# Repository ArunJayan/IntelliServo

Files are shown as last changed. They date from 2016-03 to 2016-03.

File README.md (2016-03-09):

IntelliServo
===================================================================

<p align="center">
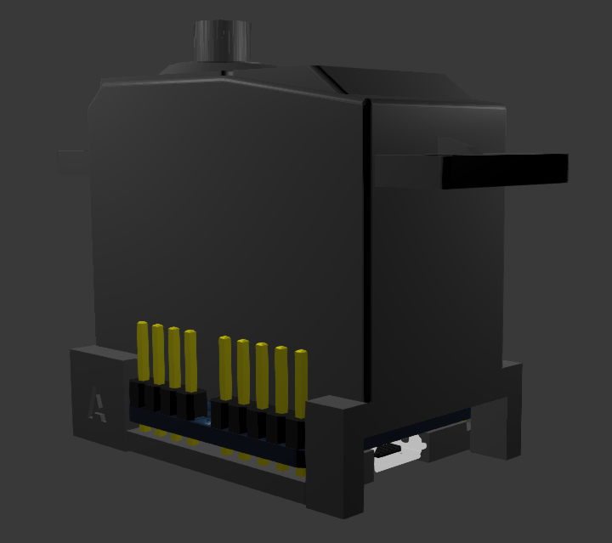
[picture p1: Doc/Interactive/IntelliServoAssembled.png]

</p>

##Overview
IntelliServo is a project aiming to transform regular hobby servos into intelligent ones by replacing their original boards. 
By doing so the servo has upgraded capabilities, such as being able to read its position, temperature and current consumption. 
Multiple servos can now be daisy-chained and controlled over I2C from a microcontroller, or over USB from a computer.

Each board features an LPC11U24 microcontroller, a DRV8837 motor driver, a TMP36 temperature sensor and a PCA9508 I2C repeater.
Each servo is unique, and so the list of compatible servos will expand with the community, so don't hesitate to add your servo!

<div style="width: 100%; display: table;">
<div style="display: table-row">

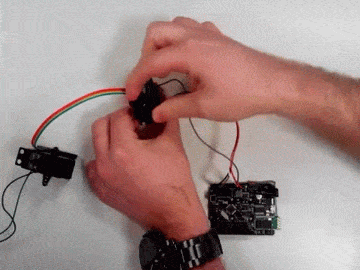
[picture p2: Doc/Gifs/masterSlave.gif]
<div align="center" style="display: table-cell;"><p align="center"><a href="https://youtu.be/W2uScJmLD4c" target="_blank">Master/Slave configuration</a></p></div>

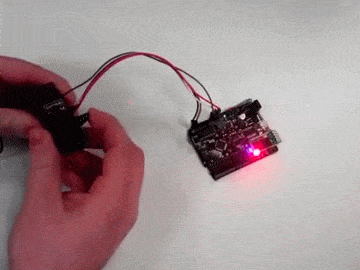
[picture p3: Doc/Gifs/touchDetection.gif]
<div align="center" style="display: table-cell;">
<p align="center"><a href="https://youtu.be/FjYgxcrhwy4" target="_blank">Touch detection</a></p>
</div>

</div>
</div>

##Connections
V_BAT: Main power line, energizes the motor and all the servo's ICs. Works between 5 and 12 volts.
V_I2C: Voltage reference for the I2C bus and powers components on the auxiliary bus. Must be 3.3V or 5V.

The servo has different connector groups:
* Main bus (5 lines): It is used to power and control the servos in daisy-chain configuration, attaching each one's A side to the previous' B side.
* Auxiliary bus (4 lines): Its function is to provide an extra link to the I2C bus, to allow other devices to be used at the same time.
* Power bus (2 lines): The main bus can be powered from the power bus on any servo, or from the last servo's main bus V_BAT and GND.
* Micro USB: Used both to upload the firmware to the board as to use it to control the servo directly from the PC, without involving other microcontrollers.

<p align="center">
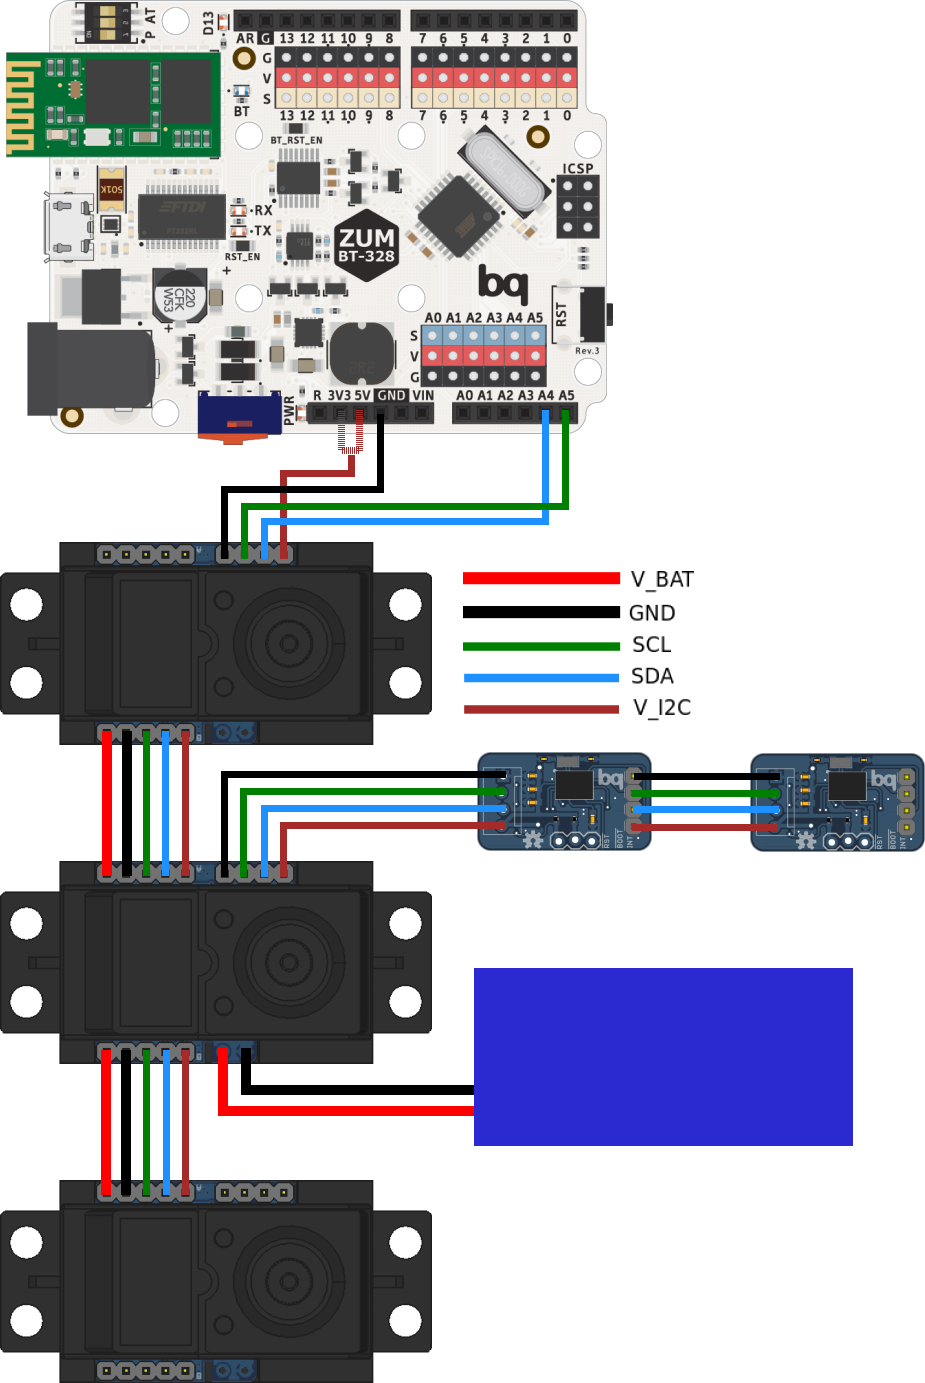
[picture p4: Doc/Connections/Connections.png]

</p>

##Installing Firmware
The board runs the firmware included in the Software/Firmware section. It is written in C++ and uses Mbed, to upload it connect the board over USB and then power it using the V_BAT and GND lines while pressing the button. 

To compile it use the "mBuino" Mbed platform, which uses the smaller LPC11U24FHI33/301 model instead of the larger LPC11U24FBD64/401 model normally used in other boards. This is important because the EEPROM memory maps are different between both and the board won't be able to access the EEPROM until the right platform is chosen.

<p align="center">
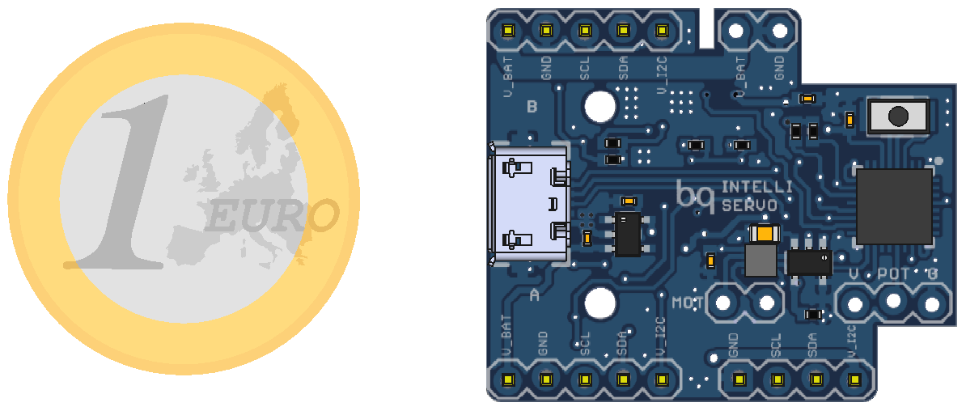
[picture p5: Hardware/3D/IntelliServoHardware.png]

</p>

##Library
The servos are controlled over I2C, but to simplify their use an arduino library with all the relevant functions and some example sketches are included as well. 
To install it simply copy it to the "sketchbook/libraries/" folder. 

##Specifications
V_BAT:&nbsp;&nbsp;&nbsp;&nbsp;&nbsp;5V-12V
V_I2C:&nbsp;&nbsp;&nbsp;&nbsp;&nbsp;&nbsp;&nbsp;3.3V/5V
I_Servo:&nbsp;&nbsp;&nbsp;&nbsp;1.8A max
I_Line:&nbsp;&nbsp;&nbsp;&nbsp;&nbsp;&nbsp;&nbsp;5A max (60mil trace)

##Contributing
This project is open-source and as so everyone is welcome to contribute. The most useful way of doing so is perhaps by expanding the list of compatible servos, by finding the moving range in degrees and PID parameters specific for each servo.

To do so add the servo to the IntelliServoConfig.h file as below

```cpp
//Added by username
#ifdef NAME_OF_SERVO
    float maxAngle=XXX;
    float Kp=XXX, Kd=XXX, Ki=XXX;
#endif
```
and to the IntelliServoMain.cpp file
```cpp
//#define NAME_OF_SERVO
```

##License
This project is licensed under Creative Commons Attribution-ShareAlike 4.0 International (CC BY-SA 4.0)

<p align="center">

</p>

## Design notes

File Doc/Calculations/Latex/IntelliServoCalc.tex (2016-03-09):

\documentclass[11pt]{article}
\usepackage[a4paper, total={17cm, 25cm}]{geometry}

\usepackage{graphicx}
\usepackage{mathtools}
\usepackage{listings}
\usepackage{color}
\definecolor{dkgreen}{rgb}{0,0.6,0}
\definecolor{gray}{rgb}{0.5,0.5,0.5}
\definecolor{mauve}{rgb}{0.58,0,0.82}
\lstset{
  language=Java,
  aboveskip=1mm,
  belowskip=1mm,
  showstringspaces=false,
  columns=flexible,
  basicstyle={\small\ttfamily},
  numbers=none,
  numberstyle=\tiny\color{gray},
  keywordstyle=\color{blue},
  commentstyle=\color{dkgreen},
  stringstyle=\color{mauve},
  breaklines=true,
  breakatwhitespace=true,
  tabsize=3
}

\begin{document}
\thispagestyle{empty}

\begin{center}
 
\hspace{-8.5cm}{
\begin{minipage}[]{\linewidth}% to keep image and caption on one page
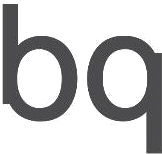
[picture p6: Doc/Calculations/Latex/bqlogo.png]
\center 
\end{minipage}
\hspace{3.5cm}Alvaro Ferr\'an Cifuentes
}

\vspace{1.75cm}
\textsc{\Huge Hardware Calculations}

\end{center}

\bigskip \flushleft

This document's purpose is to explain the current sensor calculations and the temperature sensor's equation.

\section*{Current Sensor}
Since the board uses a TI DRV8837 motor driver with a 1.8A maximum current, that is the range the LPC11U24's ADC should work in.\\[0.25cm]

To measure the current used by the motor a  10m$\Omega$ shunt resistor (R5) is added between the driver's GND pin and the ground plane. From Ohm's Law, for every 1000mA through the resistor there is a 10mV voltage drop, which means an 18mV range.\\[0.25cm]

The ADC works between 0 and 3.3V and has a 10-bit resolution, or a 3.23mV/step resolution. With this setup only the first 6 steps of the 1024 would be meaningful, which is a meager 0.6\% of the ADC's scale. 

\vspace{0.5cm}
\begin{minipage}[]{\linewidth}% to keep image and caption on one page
\center 
\end{minipage}
\\[0.5cm]

To use the ADC's full scale the resistor's voltage range must be transformed to that of the ADC, which is done by multiplying by the operational amplifier's gain G.

\center $G=\frac{3300}{18}=183.33$

\flushleft To get such gain the OpAmp is configured as a non-inverting amplifier, as seen in the following image:

\vspace{0.5cm}
\begin{minipage}[]{\linewidth}% to keep image and caption on one page
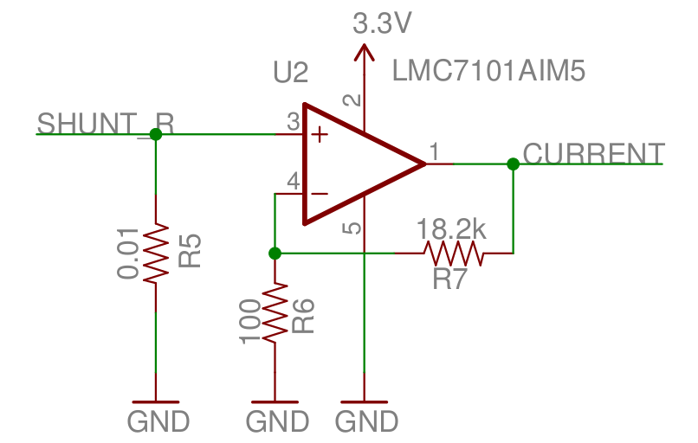
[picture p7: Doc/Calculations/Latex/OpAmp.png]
\center 
\end{minipage}
\\[0.5cm]

\center $G=1+\frac{R7}{R6}$
\center $G=1+\frac{18.2k}{100}$
\\[0.4cm]

The ADC will now use its full scale to read the current, with a theoretical resolution of 1.76mA/step.

\newpage \thispagestyle{empty}
\bigskip \flushleft

\section*{Temperature Sensor}
The board includes a TMP36 temperature sensor from Analog Devices. From its datasheet:

\vspace{0.5cm}
\begin{minipage}[]{\linewidth}% to keep image and caption on one page
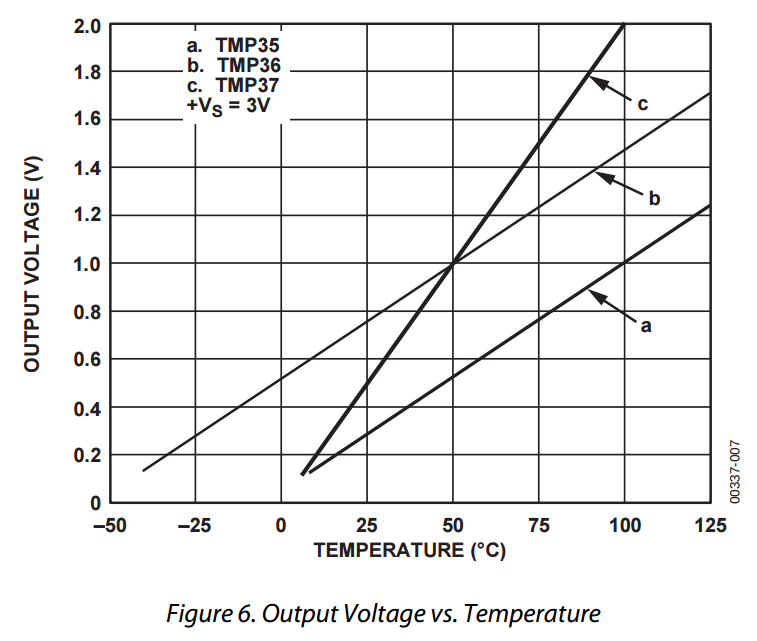
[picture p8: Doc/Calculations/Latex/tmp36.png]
\center 
\end{minipage}
\\[0.5cm]

and TMP36 Output Voltage when T=25$^\circ$C is 750mV. Knowing this, the temperature equation is calculated:

\center $V(mV)=m\cdot T(^\circ C)+p$
\center $m=\frac{1000-750}{50-25}=10$
\center $p=V-m\cdot T=750-10\cdot25=500$
\center $V(mV)=10\cdot T(^\circ C)+500$
\\[1cm]
\center $\rightarrow T(^\circ C)= (V(mV)-500)/10$

\end{document}

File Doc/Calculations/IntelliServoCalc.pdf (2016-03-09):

Alvaro Ferr´an Cifuentes

## Hardware Calculations

This document’s purpose is to explain the current sensor calculations and the temperature sensor’s equation.

## Current Sensor

Since the board uses a TI DRV8837 motor driver with a 1.8A maximum current, that is the range the LPC11U24’s ADC should work in.

To measure the current used by the motor a 10mΩ shunt resistor (R5) is added between the driver’s GND pin and the ground plane. From Ohm’s Law, for every 1000mA through the resistor there is a 10mV voltage drop, which means an 18mV range.

The ADC works between 0 and 3.3V and has a 10-bit resolution, or a 3.23mV/step resolution. With this setup only the first 6 steps of the 1024 would be meaningful, which is a meager 0.6% of the ADC’s scale.

To use the ADC’s full scale the resistor’s voltage range must be transformed to that of the ADC, which is done by multiplying by the operational amplifier’s gain G.

G =

3300
18 = 183.33

To get such gain the OpAmp is configured as a non-inverting amplifier, as seen in the following image:


G = 1 + R7
R6
G = 1 + 18.2k
100

The ADC will now use its full scale to read the current, with a theoretical resolution of 1.76mA/step.

## Temperature Sensor

The board includes a TMP36 temperature sensor from Analog Devices. From its datasheet:


and TMP36 Output Voltage when T=25◦C is 750mV. Knowing this, the temperature equation is calculated:

V (mV ) = m · T(

◦C) + p

m =

1000−750
50−25 = 10

p = V − m · T = 750 − 10 · 25 = 500

V (mV ) = 10 · T(

◦C) + 500

→ T(

◦C) = (V (mV ) − 500)/10

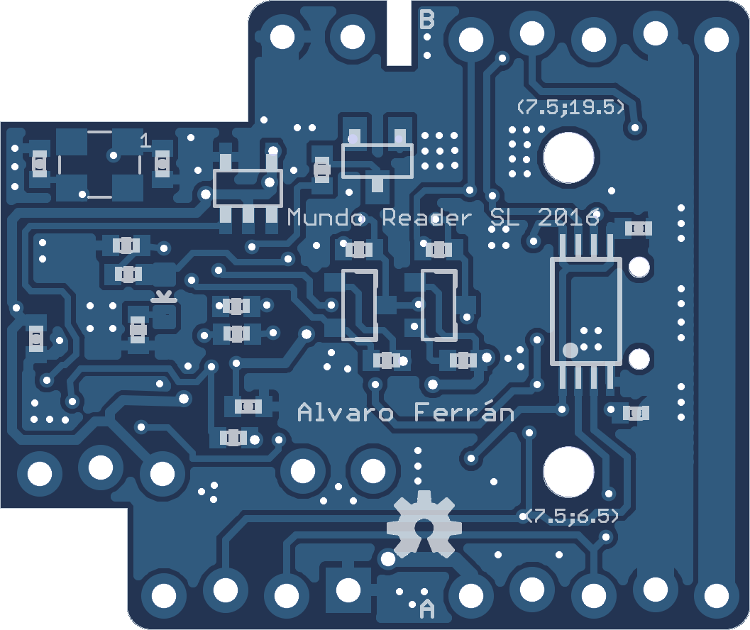
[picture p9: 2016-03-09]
Hardware/Eagle/Silkscreen/Silkscreen2-Bottom.png

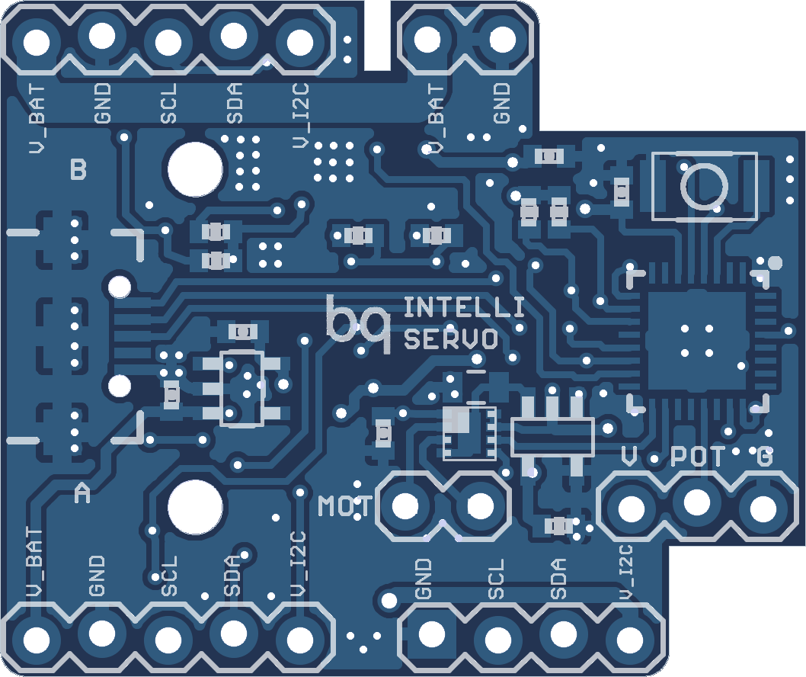
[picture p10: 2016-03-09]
Hardware/Eagle/Silkscreen/Silkscreen1-Top.png

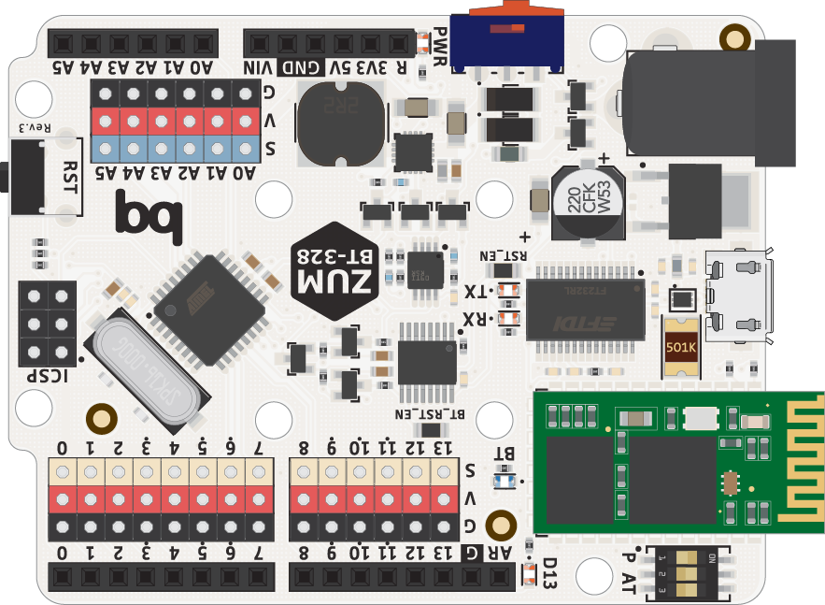
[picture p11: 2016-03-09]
Doc/Connections/DiaImgs/zumbt.png

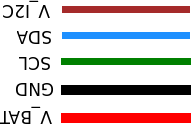
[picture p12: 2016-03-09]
Doc/Connections/DiaImgs/Legend.png

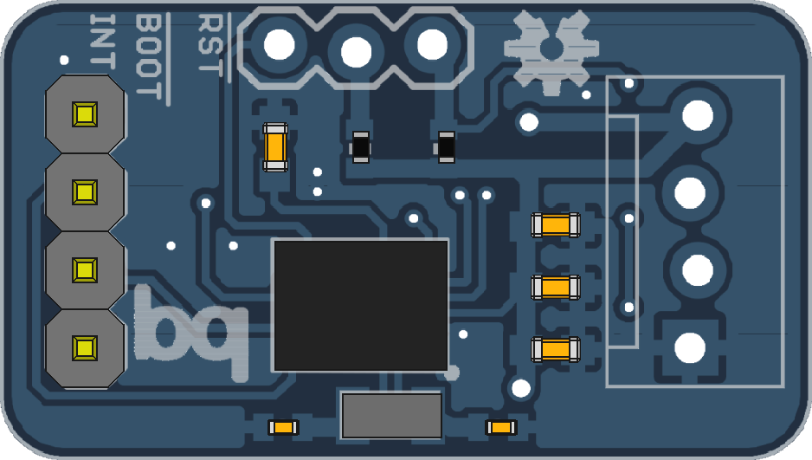
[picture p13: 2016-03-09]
Doc/Connections/DiaImgs/BNO055.png

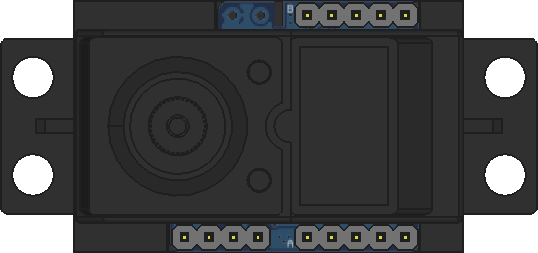
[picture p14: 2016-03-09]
Doc/Connections/DiaImgs/servo.png

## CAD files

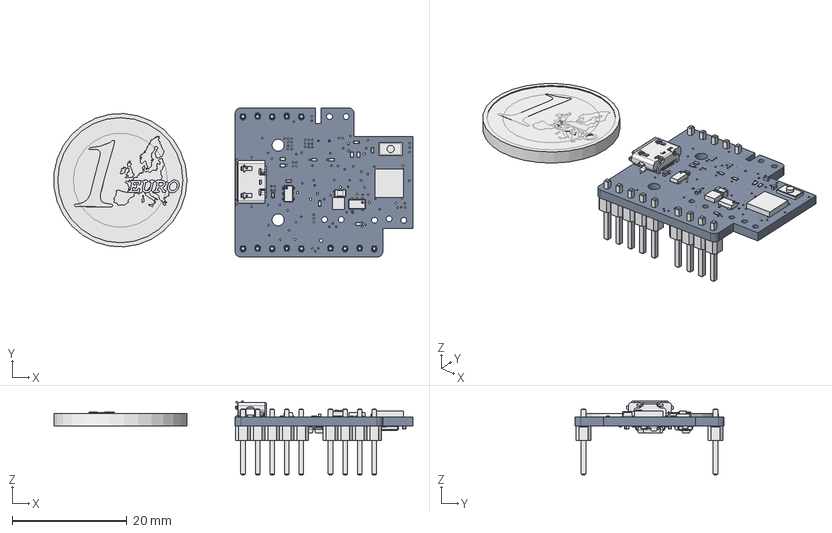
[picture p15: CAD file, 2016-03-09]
Hardware/3D/IntelliServoHardware.fcstd
62.6 x 26.0 x 12.9 mm
Board
Q2
C11
C3
C7
C8
C9
C10
C6
C4
C2
C1
C5
IC3
LED1
Q3
R5
R9
R10
R16
R15
R18
R12
R7
R6
R1
R2
R3
R4
R14
R13
R8
R11
R17
R19
SW1
U1
U2
U3
IC2
IC1
JP7
Q1
Q4
1x5pins
1x5pins001
1x4pins
Euro

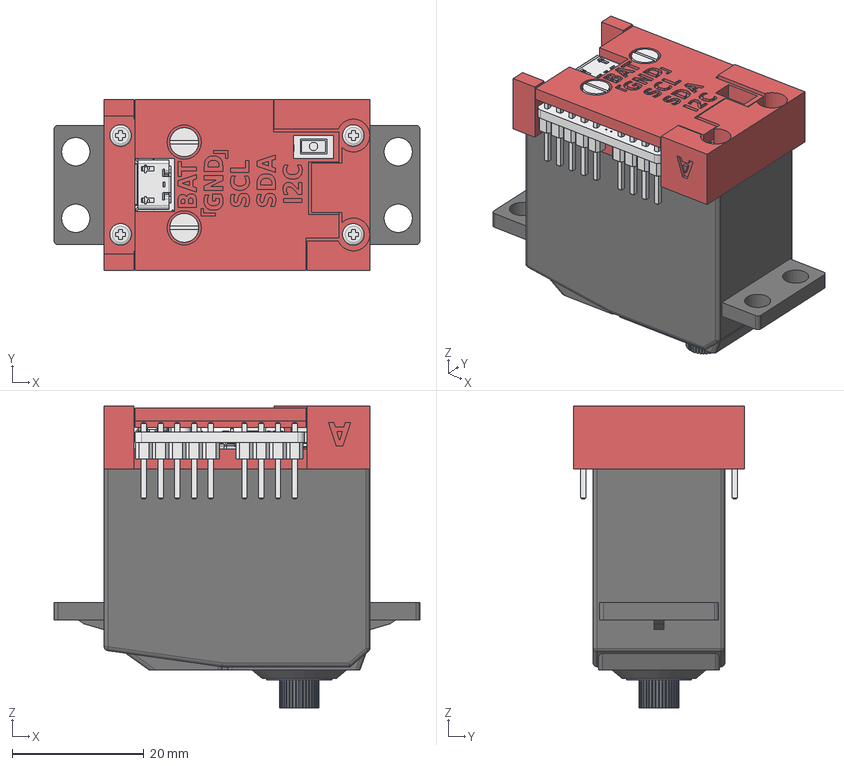
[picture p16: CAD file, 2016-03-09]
Mechanical/IntelliServoMechanical.fcstd
55.5 x 26.0 x 45.7 mm
FutabaS3003-screws
FutabaS3003
PCB-screws
base-src
cover-src
PCB

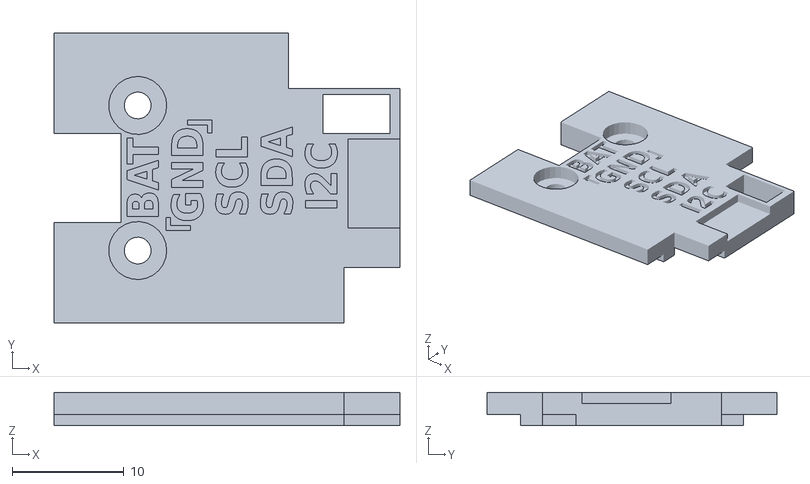
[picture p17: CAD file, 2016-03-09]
Mechanical/STL/cover.stl
31.0 x 26.0 x 3.00

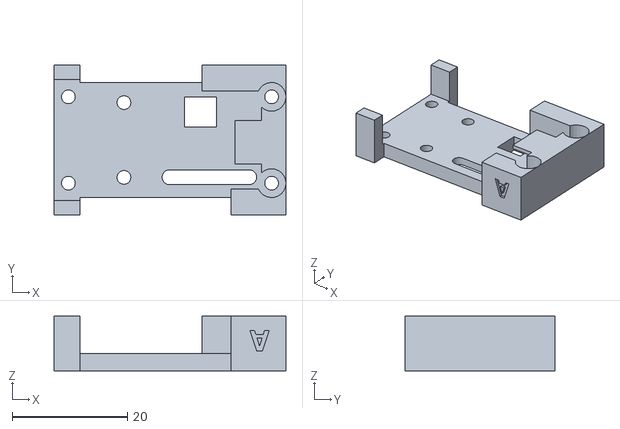
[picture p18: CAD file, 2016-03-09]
Mechanical/STL/base.stl
40.3 x 26.0 x 9.50

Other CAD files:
Hardware/Eagle/Outline/IntelliServoOutline.fcstd
Doc/Interactive/IntelliServoBoard.blend
Hardware/Eagle/Outline/IntelliServoOutline.dxf

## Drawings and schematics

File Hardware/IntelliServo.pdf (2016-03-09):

# R7 R⁶ U3

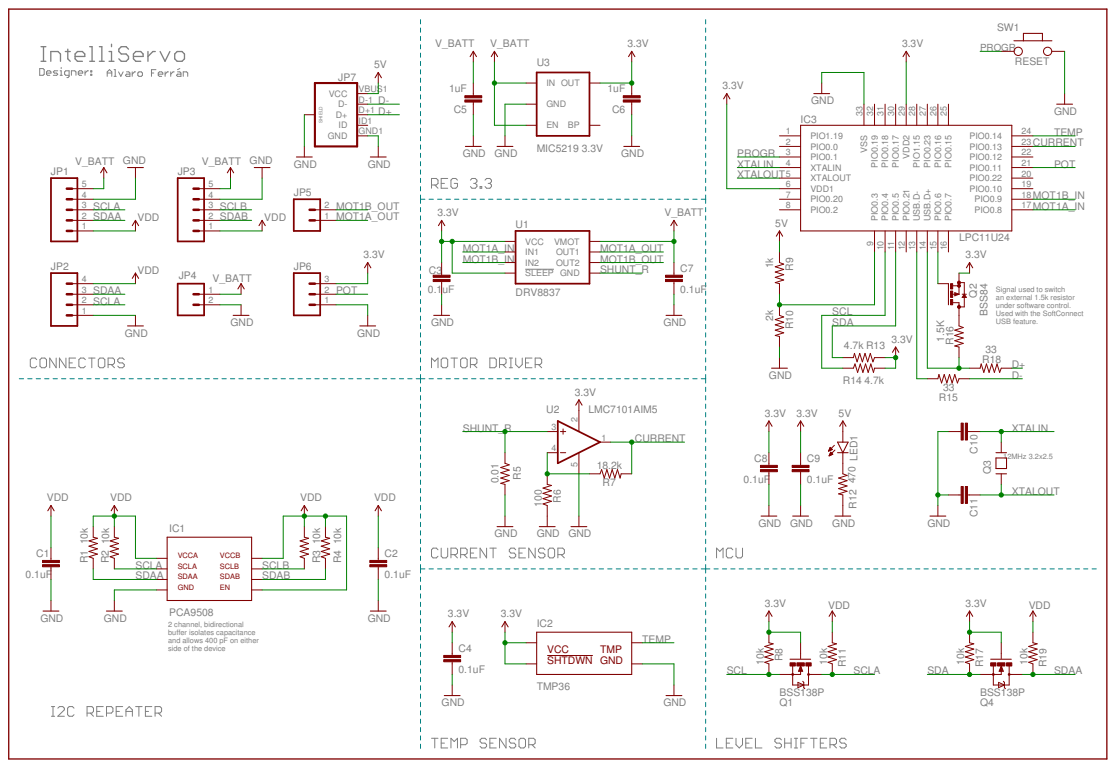
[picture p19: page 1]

BSS84
Signal used to switch
an external 1.5k resistor under software control. Used with the SoftConnect USB feature.

PCA9508
2 channel, bidirectional buffer isolates capacitance
and allows 400 pF on either side of the device

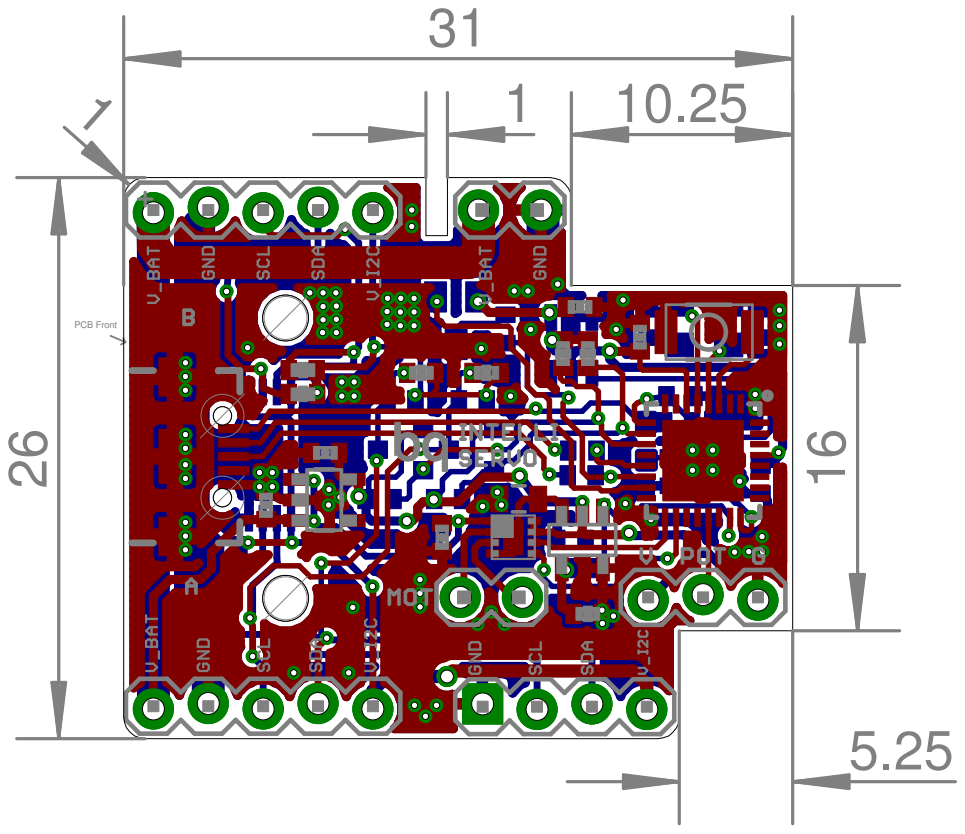
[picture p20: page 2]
PCB Front

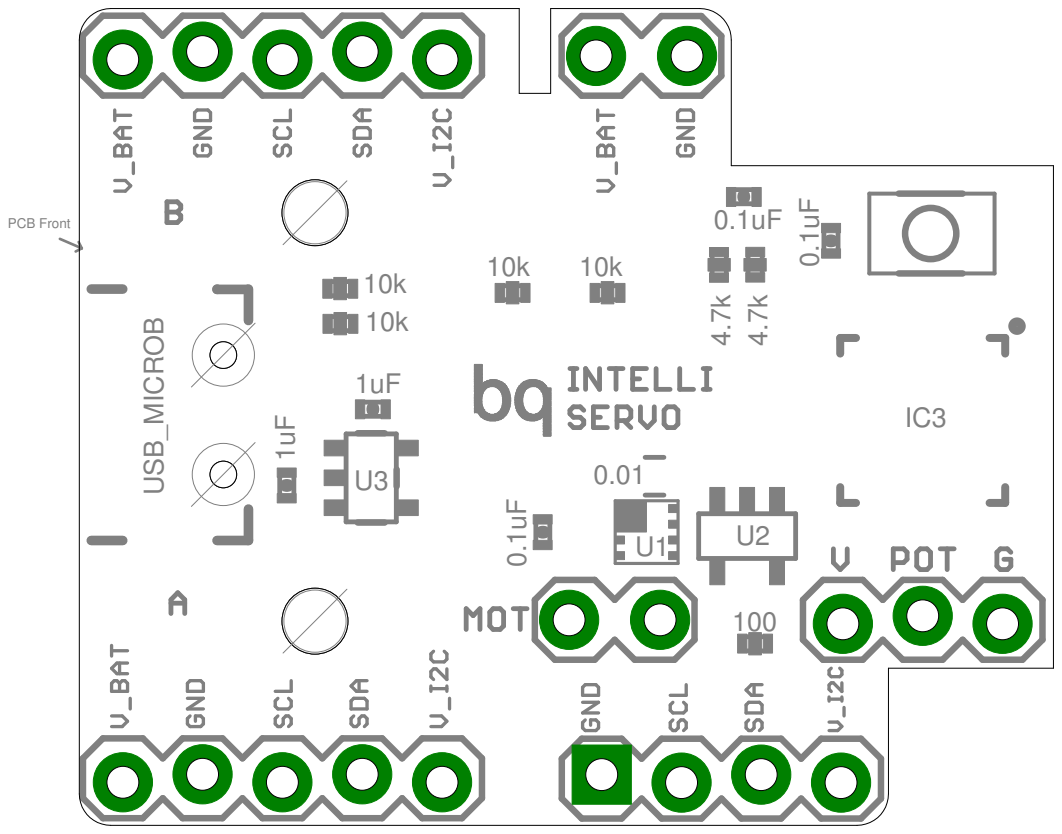
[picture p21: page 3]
PCB Front; 4.7k 4.7k USB_MICROB

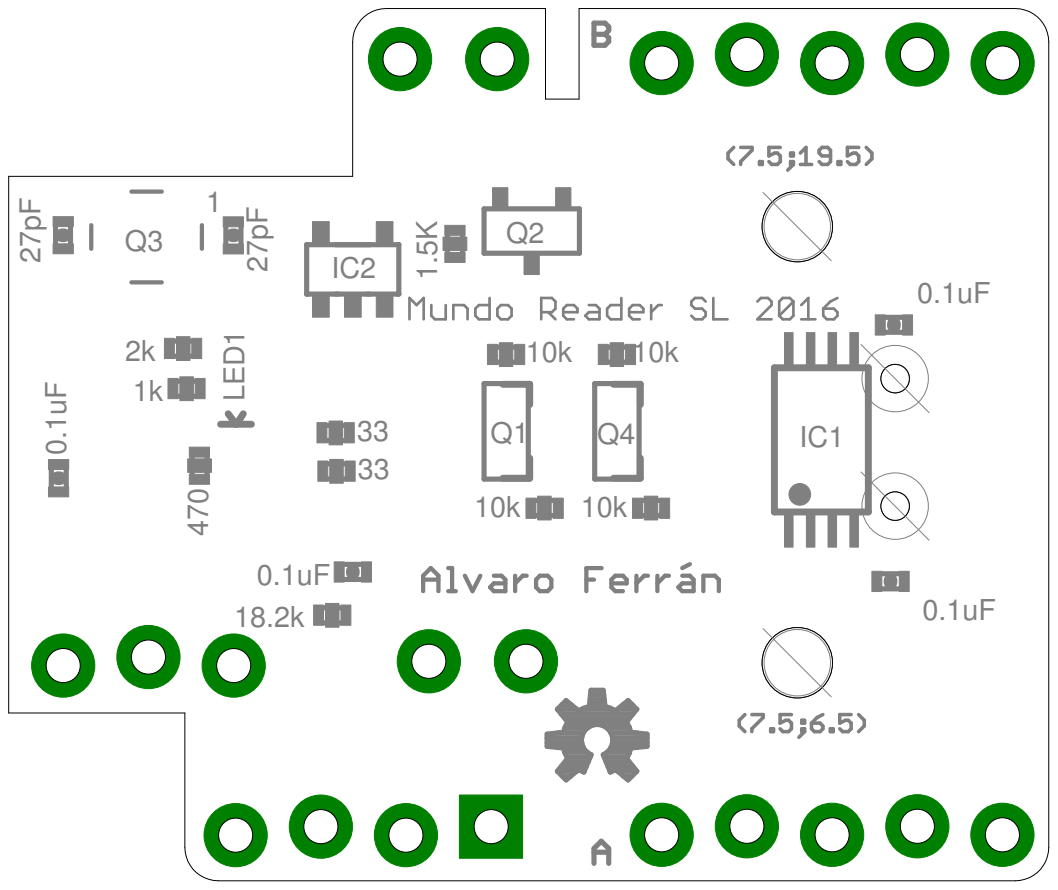
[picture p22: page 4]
1 LED¹ Q3; IC1 ²⁷pF 0.1uF ⁰.1uF 27pF

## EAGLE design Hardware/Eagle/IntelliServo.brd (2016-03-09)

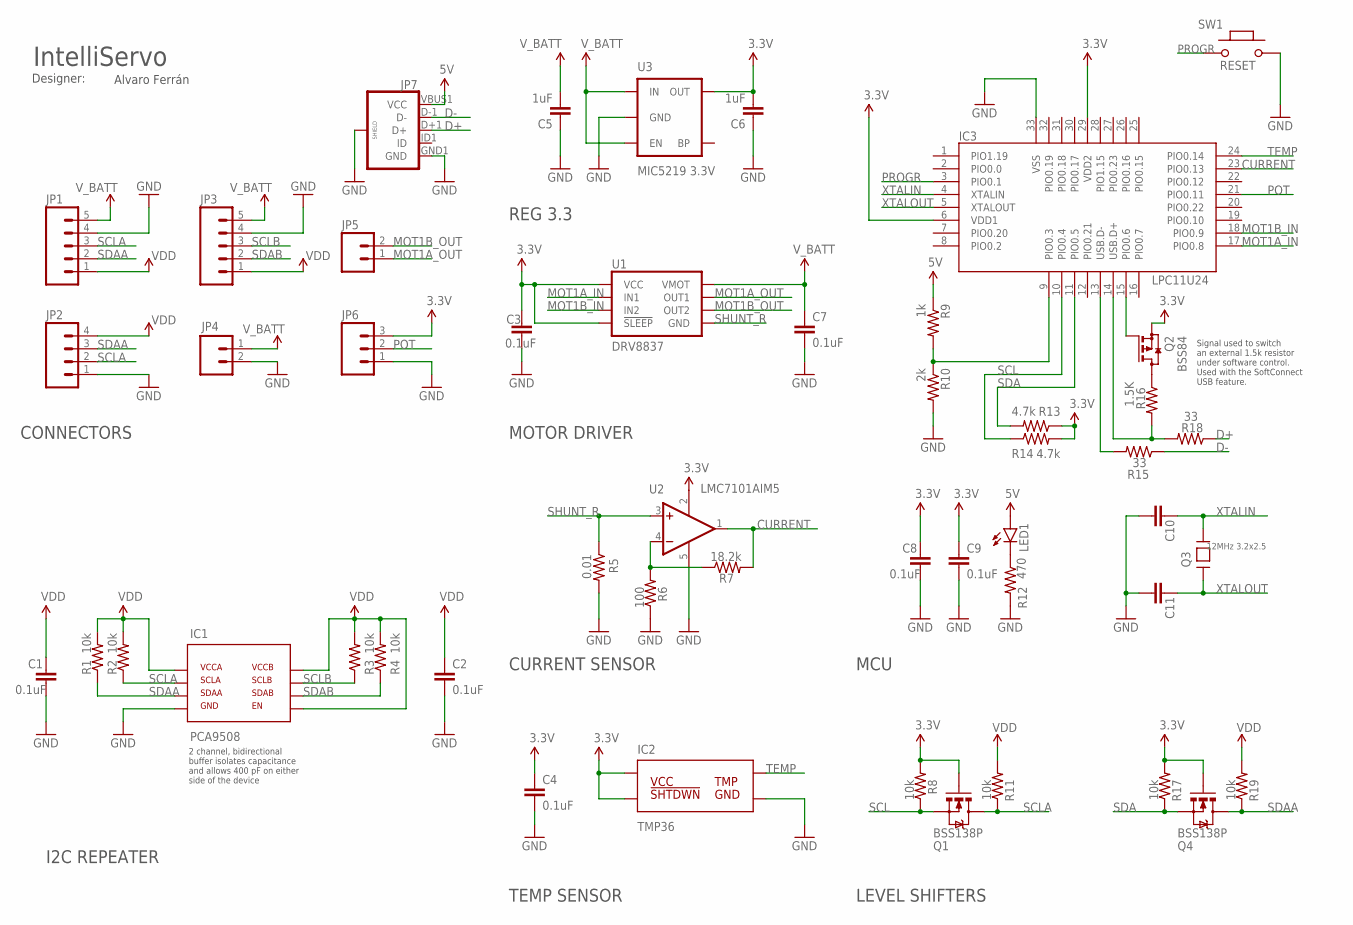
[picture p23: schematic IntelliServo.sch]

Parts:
C1, C2, C3, C4, C7, C8, C9: 0.1uF; 0402-CAP
C5, C6: 1uF; 0402-CAP
C10, C11: 27pF; 0402-CAP
IC1: PCA9508; TSSOP8
IC2: TMP36; SOT23-5
IC3: LPC11U24; HVQFN33_5X5MM
JP1, JP3: M05LOCK; 1X05_LOCK
JP2: M04LOCK; 1X04_LOCK
JP4, JP5: M02LOCK; 1X02_LOCK
JP6: M03LOCK; 1X03_LOCK
JP7: USB_MICROB; USB-B-MICRO-SMD_V03
LED1: LED0603; LED-0603
Q1, Q4: BSS138P; SOT23-3
Q2: BSS84; SOT23
Q3: 12MHz 3.2x2.5; CRYSTAL_3.2X2.5
R1, R2, R3, R4, R8, R11, R17, R19: 10k; 0402-RES
R5: 0.01; 0805
R6: 100; 0402-RES
R7: 18.2k; 0402-RES
R9: 1k; 0402-RES
R10: 2k; 0402-RES
R12: 470; 0402-RES
R13, R14: 4.7k; 0402-RES
R15, R18: 33; 0402-RES
R16: 1.5K; 0402-RES
SW1: RESET; 157SW
U1: DRV8837; DSG
U2: LMC7101AIM5; SOT23-5
U3: MIC5219 3.3V; SOT23-5

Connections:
3.3V: C3.1, C4.1, C6.2, C8.1, C9.1, IC2.2 (VCC), IC2.4 (!SHTDWN), IC3.6 (VDD1), IC3.29 (VDD2), JP6.3, Q1.1 (G), Q2.2 (S), Q4.1 (G), R8.2, R13.1, R14.2, R17.2, U1.7 (!SLEEP), U1.8 (VCC), U2.2 (V+), U3.5 (OUT)
5V: JP7.VBUS1 (VCC), LED1.A, R9.1
CURRENT: IC3.23 (PIO0.13), R7.2, U2.1 (OUT)
D+: JP7.D+1 (D+), R18.1
D-: JP7.D-1 (D-), R15.1
GND: C1.2, C2.2, C3.2, C4.2, C5.1, C6.1, C7.2, C8.2, C9.2, C10.2, C11.2, IC1.4 (GND), IC2.5 (GND), IC3.33 (VSS), JP1.4, JP2.1, JP3.4, JP4.2, JP6.1, JP7.GND1 (GND), JP7.SHIELD1 (SHIELD), JP7.SHIELD2 (SHIELD), JP7.SHIELD3 (SHIELD), R5.2, R6.1, R10.2, R12.2, SW1.2, U2.5 (V-), U3.2 (GND)
MOT1A_IN: IC3.17 (PIO0.8), U1.6 (IN1)
MOT1A_OUT: JP5.1, U1.2 (OUT1)
MOT1B_IN: IC3.18 (PIO0.9), U1.5 (IN2)
MOT1B_OUT: JP5.2, U1.3 (OUT2)
unnamed: LED1.C, R12.1
unnamed: R6.2, R7.1, U2.4 (-IN)
unnamed: IC3.14 (USB.D+), R16.2, R18.2
unnamed: IC3.13 (USB.D-), R15.2
unnamed: Q2.3 (D), R16.1
unnamed: IC3.15 (PIO0.6), Q2.1 (G)
P0.3/ISP_COMMAND_USB_HIGH: IC3.9 (PIO0.3), R9.2, R10.1
POT: IC3.21 (PIO0.11), JP6.2
PROGR: IC3.3 (PIO0.1), SW1.1
SCL: IC3.10 (PIO0.4), Q1.2 (S), R8.1, R14.1
SCLA: IC1.2 (SCLA), JP1.3, JP2.2, Q1.3 (D), R2.1, R11.1
SCLB: IC1.7 (SCLB), JP3.3, R3.1
SDA: IC3.11 (PIO0.5), Q4.2 (S), R13.2, R17.1
SDAA: IC1.3 (SDAA), JP1.2, JP2.3, Q4.3 (D), R1.1, R19.1
SDAB: IC1.6 (SDAB), JP3.2, R4.1
SHUNT_R: R5.1, U1.4 (GND), U1.PAD (GND), U2.3 (+IN)
TEMP: IC2.1 (TMP), IC3.24 (PIO0.14)
VDD: C1.1, C2.1, IC1.1 (VCCA), IC1.5 (EN), IC1.8 (VCCB), JP1.1, JP2.4, JP3.1, R1.2, R2.2, R3.2, R4.2, R11.2, R19.2
V_BATT: C5.2, C7.1, JP1.5, JP3.5, JP4.1, U1.1 (VMOT), U3.1 (IN), U3.3 (EN)
XTALIN: C10.1, IC3.4 (XTALIN), Q3.3
XTALOUT: C11.1, IC3.5 (XTALOUT), Q3.1

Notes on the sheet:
Designer:
Alvaro Ferrán
IntelliServo
REG 3.3
MCU
MOTOR DRIVER
Signal used to switch an external 1.5k resistor under software control. Used with the SoftConnect USB feature.
CURRENT SENSOR
TEMP SENSOR
CONNECTORS
LEVEL SHIFTERS
I2C REPEATER
2 channel, bidirectional buffer isolates capacitance and allows 400 pF on either side of the device
PCA9508
IC2
TMP36
IC1

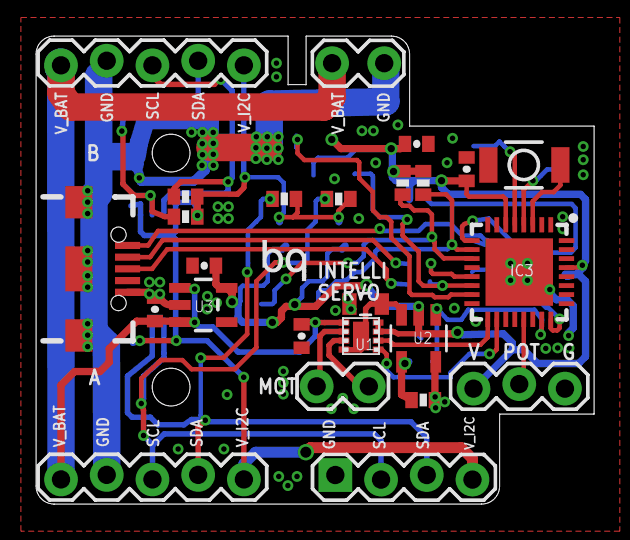
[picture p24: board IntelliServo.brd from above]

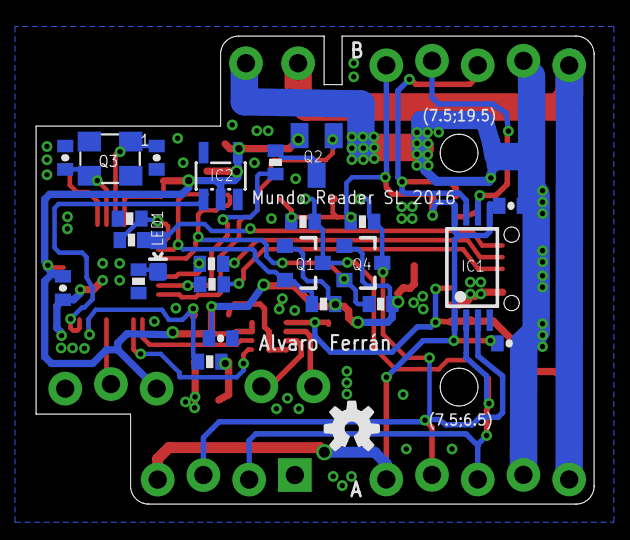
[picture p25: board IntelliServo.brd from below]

Board: 2 copper layers, 31.0 x 26.0 mm, 51 parts (25 on the bottom side), 31 nets.

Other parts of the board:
U$1: BQ_LOGO_SMALL_1
U$2: OSHW-LOGO-S

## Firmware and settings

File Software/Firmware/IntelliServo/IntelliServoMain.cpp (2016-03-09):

//--------------------------------------------------------------
//--    IntelliServo
//--    I2C servo with temperature and current sensors
//--------------------------------------------------------------
//--    BQ
//--------------------------------------------------------------
//--    Firmware created by 
//--        Alvaro Ferran Cifuentes (alvaroferran)
//--------------------------------------------------------------
//--    Released on March 2016
//--    under the GPL v3
//--------------------------------------------------------------

//Select servo
#define FUTABA_S3003
//#define TURNIGY_1268HV



#include "mbed.h"
#include "USBSerial.h"
#include "IAP.h"
#include "IntelliServoConfig.h"
#define constrain(amt,low,high) ((amt)<(low)?(low):((amt)>(high)?(high):(amt)))

//EEPROM values
#define     TARGET_ADDRESS  64 //First non-reserved address in EEPROM
#define     BYTE_SIZE       1

//USBSerial pc;
IAP     iap;

I2CSlave slave(P0_5, P0_4); //SDA, SCL

PwmOut mot1(P0_8);
PwmOut mot2(P0_9);
AnalogIn   pot(P0_11);
AnalogIn   current(P0_13);
AnalogIn   temperature(P0_14); 

void setAngle(int16_t);
int16_t getAngle();
int16_t getCurrent();
int16_t getTemp();
void changeAddress(uint8_t);
void setEepromByte(int, uint8_t);
uint8_t getEepromByte(int);
int eepromAddres=1; //After TARGET_ADDRESS



/********MAIN***************************************************************/

int main() {
    
    char inI2C[10];
    char outI2C[2];
    int8_t slaveRegister;
    int16_t angleIn, angleOut, currentOut, tempOut;
    bool angleSet=false;
    int8_t disable=1;
    
    mot2.period_us(33.33f);  // 30kHz 
    mot1.period_us(33.33f);  
    mot1.write(0.00f);
    mot2.write(0.00f);

    //Uncomment to reset default i2c address
    //setEepromByte(PLACE,(uint8_t) 0x01);

    uint8_t inValue, i2cAddress=0x02;
    inValue=getEepromByte(eepromAddres);
    if(inValue!= (uint8_t) 0 ) i2cAddress=inValue; 
    slave.address(i2cAddress<<1);    


    while(1){     
             
        int i = slave.receive();
        switch (i) {           
            
            case I2CSlave::WriteAddressed:      //Receive
                
                slave.read(inI2C, 10);
                slaveRegister=inI2C[0];

                switch(slaveRegister){
                    case 0x0A:  //Change address
                        changeAddress(inI2C[1]);
                    break;
                    
                    case 0x01:  //Disable motor
                        disable=inI2C[1];
                    break;
                    
                    case 0x02:  //Set angle
                        angleIn=(int16_t)  (inI2C[1] << 8) | inI2C[2];
                        disable=0; 
                        angleSet=true;
                    break;
                }
                
                
            break;
            
            
            case I2CSlave::ReadAddressed:       //Reply
                               
                switch(slaveRegister){
                    case 0x04:  //Get angle
                        outI2C[0]= (angleOut >> 8) & 0xFF;
                        outI2C[1]= angleOut & 0xFF;
                    break;
                    
                    case 0x06:  //Get current
                        outI2C[0]= (currentOut >> 8) & 0xFF;
                        outI2C[1]= currentOut & 0xFF;
                    break;
                    
                    case 0x08:  //Get temperature
                        outI2C[0]= (tempOut >> 8) & 0xFF;
                        outI2C[1]= tempOut & 0xFF;
                    break;
                }
                
                slave.write(outI2C, 2); 
                
            break;
            
        }
        for(int i = 0; i < 10; i++) inI2C[i] = 0;  
        
       
        
       //Keep setting the angle so the servo stays energized
       if(angleSet==true){ //Make sure servo only starts moving when a value has been sent
            if(disable==0)
                setAngle(angleIn);
            else {
                mot1.write(0.00f);
                mot2.write(0.00f);
            }
       }
        
       angleOut=getAngle();
       currentOut=getCurrent();
       tempOut=getTemp();
    
      
    }
    
}






/********SET ANGLE**********************************************************/
//PID setting based on Angel Espeso's example (http://roble.uno/control-pid-barra-y-bola-arduino/)

void setAngle(int16_t desiredAngle){

    desiredAngle=constrain(desiredAngle,-1,maxAngle);  //Limit legal angles
    
    int16_t currentAngle=0, lastAngle, error=0, lastError;
    int eCount=0;
    float I=0;
    while(1){
        
        wait_ms(1);
        
        //Read current angle 
        lastAngle=currentAngle;
        currentAngle=getAngle();
        
        //Error
        lastError=error;
        error=desiredAngle-currentAngle;
        
        //Calculate average speed
        float v[5];   //Speed vector
        for (int i=0; i<5; i++) // Move all speed values one space to the left to make space for the newest one
            v[i] =v [i+1];
        v[4] = (error-lastError); // Add last speed
        float vel=0;
        for (int i=0; i<5; i++)     // Average speed
            vel += v[i];
        vel /= 5;
        vel/=100;
                
        //I 
        if(abs(error)<10 && abs(error)>0.2)
            I+=error*Ki;
        else 
            I=0;
        
        //Voltage calculation
        float pwr=Kp*error+Kd*vel+I;
        
        //Motor control
        float speed=0;//0.06; 
        if(pwr>0){
            mot1.write(1-(abs(pwr)+speed)); 
            mot2.write(1); 
        }else {
            mot2.write(1-(abs(pwr)+speed)); 
            mot1.write(1);
        }
        
        //pc.printf("Pot Angle: %d   Pwr: %.2f  Current: %.2f\n" ,currentAngle ,abs(pwr)+speed ,current.read()*100/0.055);
    
        //Angle stable
        if(abs(currentAngle-lastAngle)<=1){     //Difference in angle instead of error to avoid blocking when angle is not recheable
            eCount++;
            if(eCount>5) 
                break;
        }
        
        
    }
}



/********GET ANGLE**********************************************************/

int16_t getAngle(){
    float aF=0;
    int16_t aI=0;
    for(int i=0; i<5; i++)
         aF+=(pot.read()*100-5)*2.439; 
    aI=(int16_t)constrain(aF/5,0,maxAngle);
    return aI;
}



/********GET CURRENT*********************************************************/

int16_t getCurrent(){
    float cF=0;
    int16_t cI=0;
    for(int i=0; i<5; i++)
         cF+=current.read()*100/0.055; 
    cI=(int16_t)cF/5;
    return cI;
}






/********GET TEMPERATURE****************************************************/

int16_t getTemp(){ 
    return (int16_t) (temperature.read()*3300-500)/10;
}




/********CHANGE ADDRESS*****************************************************/

void changeAddress(uint8_t address){
    setEepromByte(eepromAddres, address);
    slave.address(address<<1);  
}


/********EEPROM R&W*********************************************************/
//EEPROM acces code based on Dave Tech's example (https://developer.mbed.org/users/kstech/code/EepromTest/)

typedef union data {
    uint8_t b;
    char  s[1];
} myData; 

  
void setEepromByte(int place, uint8_t incomingByte){
    myData setByte;
    char someBytes[1];
    setByte.b = incomingByte;
    for(int i=0; i<sizeof(someBytes); i++)
        someBytes[i]=setByte.s[i];
    iap.write_eeprom( someBytes, (char*) (TARGET_ADDRESS+place), BYTE_SIZE );
} 
 
uint8_t getEepromByte(int place){
    myData getByte;
    char someBytes[1];
    iap.read_eeprom( (char*)(TARGET_ADDRESS+place), someBytes, BYTE_SIZE );
    for(int i=0; i<sizeof(someBytes); i++)
        getByte.s[i]=someBytes[i];
    return getByte.b;
}

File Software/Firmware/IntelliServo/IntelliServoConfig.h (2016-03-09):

//--------------------------------------------------------------
//--    IntelliServo
//--    I2C servo with temperature and current sensors
//--------------------------------------------------------------
//--    BQ
//--------------------------------------------------------------
//--    Firmware created by 
//--        Alvaro Ferran Cifuentes (alvaroferran)
//--------------------------------------------------------------
//--    Released on March 2016
//--    under the GPL v3
//--------------------------------------------------------------

#ifdef FUTABA_S3003
    float maxAngle=200;
    float Kp=0.14, Kd=0, Ki= 0.0001;
#endif

#ifdef TURNIGY_1268HV  
    float maxAngle=200;
    float Kp=0.02, Kd=0, Ki= 0.0001;
#endif

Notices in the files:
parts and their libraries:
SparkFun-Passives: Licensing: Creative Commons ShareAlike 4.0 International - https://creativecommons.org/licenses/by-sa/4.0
